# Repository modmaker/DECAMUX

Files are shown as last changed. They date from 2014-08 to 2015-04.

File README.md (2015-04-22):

DECAMUX
=======
Last changed: 2015-04-22 - Updated FAQ.

**BeBoPr++ expansion board for up to 10 axes.**

||
|:-:|
|*DECAMUX with flatcable for connection to BeBoPr++*|

## Introduction

The **DECAMUX** board **doubles the number of outputs** on the **BeBoPr++**'s extension connector. Instead of the single (**J5**) expansion connector, two of these connectors are created, for **up to 10 axes**, **20 digital outputs**, or **a combination** of these (for 3 axes and 4 PWM outputs, see the [**XTRUDR**](https://github.com/modmaker/XTRUDR)). 

The tiny 1.7 x 1.1 inches (42 x 29 mm) adapter board in combination with some new PRU software allows MachineKit/LinuxCNC to control all signals simultaneously. The board has 3 connectors, one connects to the BeBoPr, the other two connect to the expansion boards.

## Announcement
The board was announced on the MachineKit mailing list:

	Hi All,

	Since the release of the BeBoPr++ I've been asked a couple of times
	whether the BeBoPr can control more than the usual 4 or 5 axes. The
	answer has often been: "Yes, in theory. You're only limited by what
	LinuxCNC/MachineKit can control". Other boards, like the CRAMPS or
	Replicape, offer extension-boards to add more axes. But these solutions
	claim more of the BeagleBone's scarce I/O pins. The amount of available
	I/O signals on P8 and P9 is a severely limiting factor. This makes it
	hard to add axes without sacrificing other functionality. There should
	be a better solution...!
	
	During the last couple of weeks I've worked on some hardware and
	software extensions that allows a single BeBoPr++ to control 10 stepper
	motors with two PEPPER boards. In theory it should be possible to extend
	this to even more (15, 20, ...) axes, if only the software were capable
	of handling it. Currently LinuxCNC/MachineKit seems (software-wise?)
	limited to 9 axes.
	
	How is it done? Normally a single PEPPER [3] stepper module connects to
	the J5 expansion connector on the BeBoPr via a 16-wire flatcable. This
	cable carries the signals for (only) 5 axes and some control (as
	documented in the BeBoPr++ manual [1]). Because I've been programming
	the PRUSS from the very beginning, I knew it was capable of doing some
	extra work. So I've modified Charles' PRU code to multiplex two sets of
	5 axes over that single cable, and built a small splitter board to
	de-multiplex those signals again. This splitter board is called the
	DECAMUX. It's now "Open Source Hardware" and available from OSH Park
	[2]. The DECAMUX connects to the BeBoPr on one side, and to two
	(identical) PEPPER boards on the other side.
	
	Since I have no hardware (machine, robot, anything) that does something
	useful with this many axes, I'm looking for volunteers. If you have a
	'many-axes' application, are interested and feel adventurous, contact me
	to see if we can do something with your application. I've got free
	(assembled) DECAMUX boards for the first two or three projects
	demonstrating 6 axes or more!
	
	Cheers,
	-- Bas
	
	[1]
	https://github.com/modmaker/BeBoPr-plus-plus/blob/master/BeBoPr%2B%2B%20User%20Manual.pdf
	[2] https://oshpark.com/shared_projects/Nn0ndOrm
	[3] https://github.com/modmaker/BeBoPr-plus-plus/wiki/PEPPER-Intro

Read the full DECAMUX thread here: https://groups.google.com/forum/#!topic/machinekit/0aYZ0jUaGkY.

## The DECAMUX hardware
||
|:-:|
|*Bare board*|

||
|:-:|
|*Bottom side with all SMD components mounted*|

|||
|:-:|:-:|
|*After mounting connectors, Top side*|*Bottom side*|

||
|:-:|
|*With cable to connect to the BeBoPr++: two expansion connectors available*|

## The DECAMUX software
The PRU code needed for to used the DECAMUX with MachineKit is available [here](https://github.com/modmaker/machinekit/tree/feature/poc-decamux). This software will be integrated in MachineKit in the near future. An updated pepper driver component and sample configurations are in the repository too.

## How to buy / build



The [DECAMUX board design](https://github.com/modmaker/DECAMUX/blob/master/pcb/DECAMUX_schematics.pdf) and [associated software](https://github.com/modmaker/machinekit/tree/feature/poc-decamux) are available as **Open Source Hardware**. Anyone used to soldering SMD components should be able to assemble this board. L, R and C components are all (large) 0805 parts, the latches are fine pitch but, when using plenty of flux, easy to solder.

The PCB design is open hardware and available as shared project at **OSH Park**. A set of 3 PCBs can be [ordered directly from OSH Park](https://oshpark.com/shared_projects/Nn0ndOrm) for less than $10 including shipping. Total BOM cost is around EUR 8-10, or $10-$15 for the complete board including cable.

## FAQ
#### Q1: Can I use the DECAMUX together with the plug-in stepper modules?
No. The DECAMUX connects to the connector for off-board stepper drivers (J5) and uses the same signals as the plug-in stepper modules. So it's physically not possible to combine both.

#### Q2: Is the pinout of the output connectors on the DECAMUX different from J5 on the BeBoPr++?
No. The signals are the same, although the voltage levels differ (see Q3 & Q4).

#### Q3: I'm using plug-in stepper modules, can I expand my system and continue to use these modules?
Yes. For this purpose the [TAKE-5](https://github.com/modmaker/TAKE-5) expansion board was made. It can hold all four modules plus one extra, for a total of five axes.

#### Q4: I am currently using brand 'XYZZY' stepper drivers with the BeBoPr. I would like to add more axes, can I use the DECAMUX?
Probably. You have to check that your drivers will work with 3.3 Volt signal levels on the inputs. The BeBoPr generates 5 Volt CMOS levels while the DECAMUX has lower, 3.3 Volt CMOS levels. Most drivers are compatible with both though.

#### Q5: Can I cascade multiple DECAMUXes to increase the number of outputs further?
Not yet, at least not with the current DECAMUX hardware and software.

#### Q6: What software can I use with the DECAMUX?
The [BeBoPr software](https://github.com/modmaker/BeBoPr) generates step signals for only four or five axes. To work with more axes, [MachineKit](http://www.machinekit.io/) with DECAMUX support is needed (see Q7).

#### Q7: Will the [modified machinekit repository](https://github.com/modmaker/machinekit) with code for the DECAMUX be part of the official code?
Yes, soon. This is work in progress (April-2015).

#### Q8: Will the DECAMUX work with the previous generation BeBoPr and BeBoPr+ boards?
Not without modifying the BeBoP, but in theory and with some hardware patches it could be made to work.

#### **Q9**: I don't want to order 3 boards (PCBs) because I only need one.
Post a message on the MachineKit list, or send me a mail and I might have a spare for sale.

#### Q10: I'm only having basic soldering skills. The latch on the DECAMUX has 0.65 mm pitch leads. Help!
I'm looking into producing an assembled version. Drop me a mail if you're interested.

#### Q11: What are the jumper settings on the BeBoPr++ when I want to use the DECAMUX?
Both JP3 and JP4 on the bootom side of the BeBoPr++ should be closed.

#### Q12: Do I need a special device tree overlay for the DECAMUX?
Yes, you need the cape-bebopr-pp overlay instead of the default cape-bebopr-brdg. If you disable the default overlay in uEnv.txt, the proper one will be loaded by the Axis startup script.

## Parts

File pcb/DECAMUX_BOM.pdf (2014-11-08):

DECAMUX BOM

Farnell
Qty Parts | Description | MANUF | PARTNO | Price | Order Code Cost
3 J1, J2, J3 | Dual row, 16way boxed header | Amphenol | T821116A1S100CEU | € 0,27 | 2215308 | € 0,81
3 L1, L2, L3 | Ferrite bead 0805, 220 Ohm, 2A | Murata | BLM21PG221SN1D | € 0,07 | 1515661 | € 0,20
2 C3, C7 | | not specified | - | € 0,03 | | € 0,06
5 C1, C4, C5, C6, C8 Capacitor 0805, 100nF/50V X7R | Murata | GRM21BR71H104KA01L | € 0,04 | 8820120 | € 0,22
1 C2 | Capacitor 0805, 2u2/10V X7R | Murata | GRM21BR71A225KA01L | € 0,11 | 1828923 | € 0,11
2 R4, R6 | Resistor 0805, 1k00 1% | not specified | - | € 0,03 | | € 0,06
4 R1, R2, R3, R5 | Resistor 0805, 10k0 1% | not specified | - | € 0,03 | | € 0,12
2 U1, U4 | | Diodes Inc | 74LVC1G57W6-7 | € 0,11 | 1893837 | € 0,21
2 U2, U3 | | Diodes Inc | 74LVC1G58W6-7 | € 0,06 | 1893839 | € 0,12

0

U6, U7 | | Texas Instruments | SN74LVC841APW | € 1,36 | 1236405 | € 0,00
2 | | NXP | 74LVC841APW,112 | € 0,83 | 2445137 | € 1,65
1 U5 | | Texas Instruments | TPS79333DBVR | € 0,61 | 1470478 | € 0,61
1 | DECAMUX PCB | OSH Park | DECAMUX_R0 | € 2,50 | | € 2,50
1 | | Amphenol | FC16150-0 | € 1,26 | 2217610 | € 1,26
| | | | | Total Cost | € 7,93

Capacitor 0805, 100pF C0G, NP0 or X7R

Low-power multiple function gate configured as 2 input AND
Low-power multiple function gate configured as 2 input AND with inverted A input
10-bit transparent latch with 5 V tolerant inputs/outputs; 3-state Ultra low-noise, high PSRR, fast RF, 200mA LDO linear regulator

Flat Cable, 2.54MM, F/F, 150MM, 16WAY

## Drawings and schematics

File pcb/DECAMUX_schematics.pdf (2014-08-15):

A

A

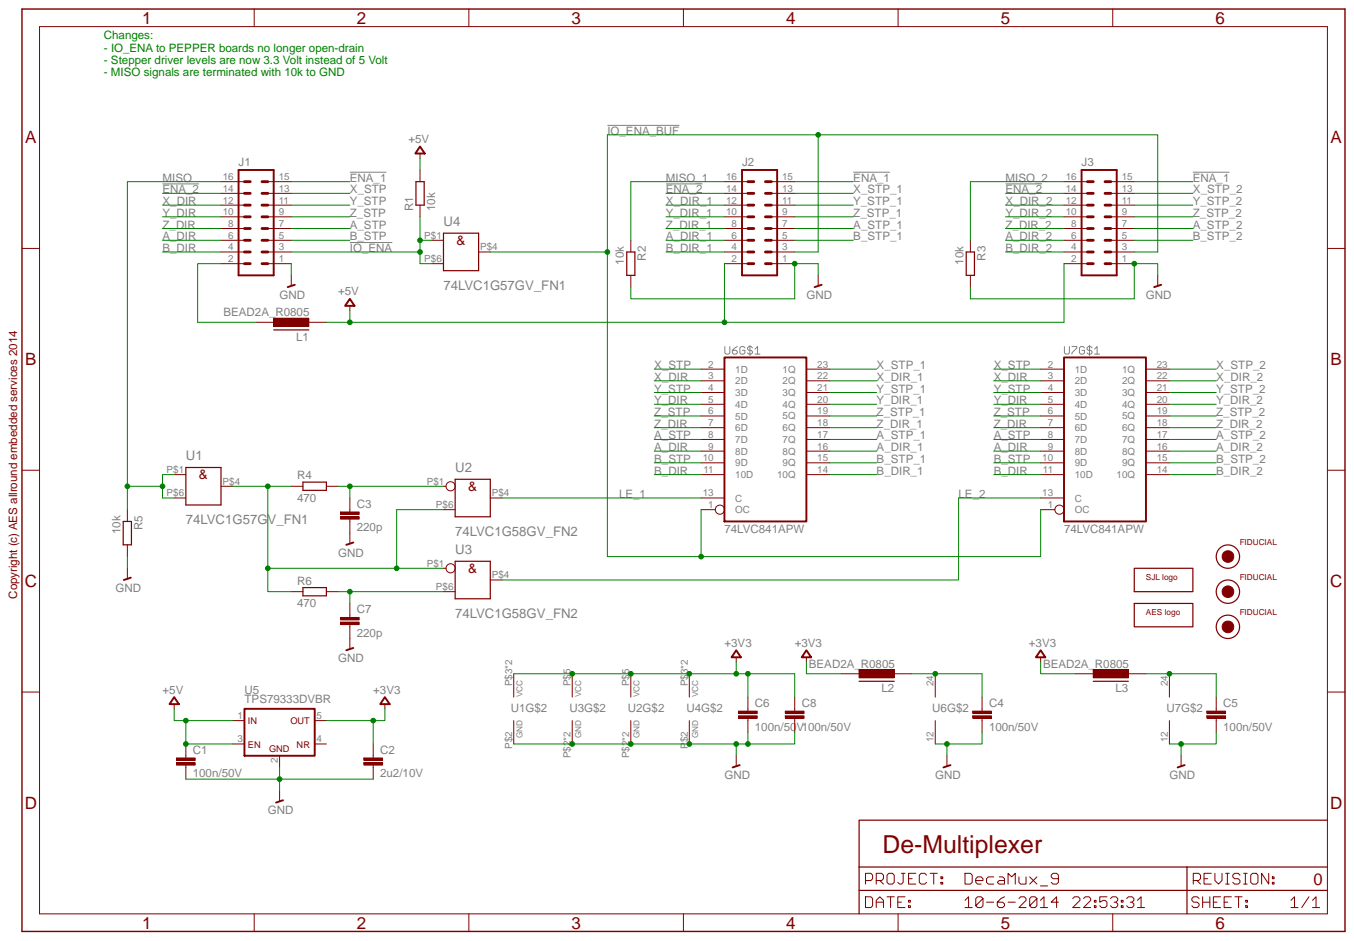
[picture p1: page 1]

Changes:
- IO_ENA to PEPPER boards no longer open-drain
- Stepper driver levels are now 3.3 Volt instead of 5 Volt
- MISO signals are terminated with 10k to GND

Copyright (c) AES allround embedded services 2014

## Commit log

2014-08-15 Added schematics of R0 board.
2014-08-15 Added Gerber files for PCB R0 4241.
    [DecaMux_9.gbl, DecaMux_9.gbo, DecaMux_9.gbs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]
2014-10-01 Added BOM for R0 board.
2014-11-08 Added alternate/cheaper latch to the BOM.
2014-11-08 Added FAQ and reference to TAKE-5 and XTRUDR boards.
